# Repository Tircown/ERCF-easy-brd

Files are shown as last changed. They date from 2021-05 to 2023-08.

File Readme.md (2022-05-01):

# ERCF EASY BRD

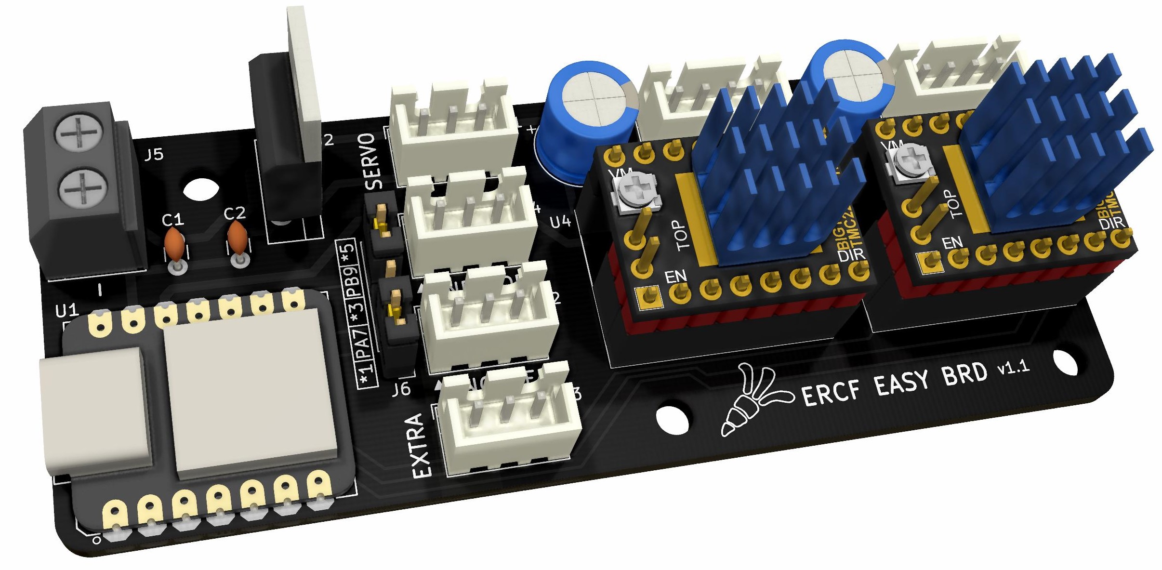
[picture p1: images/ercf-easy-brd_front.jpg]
ERCF front picture


**Be careful not to invert polarity in the screw terminal or it may damage the board and even more.**

**Do not use the servo connector as an input or do it at your own risk.\
Voltage input connected to general I/O pins may cause chip damage if it' higher than 3.3V .**

## BOM
Component | Position
------------ | -------------
Resistor 10K | R1, R2, R3, R4
Capacitor ceramic 0.33uF 25V | C1
Capacitor ceramic 0.1uF 25V | C2
Capacitor 100uF 25V | C3, C4
2P Screw terminal P=5.08 | J5
3P JST-XH male P=2.54 | J1, J2, J3, J4
4P JST-XH male P=2.54 | J6, J7
8P Header socket P=2.54 | *4x for U4 and U3*
2P Header socket P=2.54 | *1x for U4*
5P Header pin P=2.54 | J6
7P Header socket female P=2.54 | *(optionnal) 2x for Seeeduino XIAO*
Seeeduino XIAO or Adafruit QT Py (same footprint & pinout)| U1
Voltage regulator L7805CV | U2
SilentStepStick TMC2209 | U3, U4
Jumper P=2.54 | *2x for J6*
Heatsink for TO-220 | *(recommended) 1x for the L7805CP (1)*

*(1) You will need to bend a fin and remove the pin of the TO-220 heatsink. Make sure the PCB has no bare traces underneath or apply an insolator before (i.e. piece of chattertone).*

## Configure the MCU - Seeeduino XIAO
* Install bossac (version ≥1.8)
```
sudo apt install libreadline-dev libwxgtk3.0-*
git clone https://github.com/shumatech/BOSSA.git
cd BOSSA
make
sudo cp bin/bossac /usr/local/bin
```
* Prepare the firmware
```
cd ~/klipper
make menuconfig
```
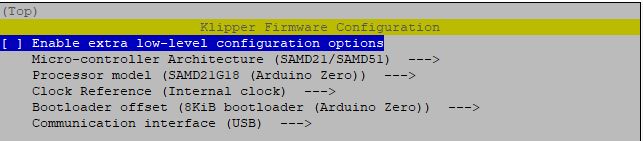
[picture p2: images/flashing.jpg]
Menuconfig instructions

```
make clean
make
```
* Flashing the Seeeduino XIAO
Connect the Seeeduino XIAO to your raspberry if it's not already done.
Get the port of the XIAO, i.e. `ls /dev/tty*`, and modify the default `/dev/ttyACM1` in the command line bellow.
Use tweezers or short lines to short the RST pins in the diagram twice. The orange LED lights flicker on and light up. Then send in the next few seconds this command line matching your port.
```
sudo /usr/local/bin/bossac -i -d -p /dev/ttyACM1 -e -w -v -R --offset=0x2000 out/klipper.bin
```

More informations on how to reset for flashing:\
https://wiki.seeedstudio.com/Seeeduino-XIAO/#enter-bootloader-mode

## Klipper configuration
See [ercf_hardware.cfg](config/Seeeduino%20XIAO%20-%20SAMD21G18/ercf_hardware.cfg) for the Seeeduino XIAO (most common solution)
Other microcontrollers configurations are available in config/

## Get the PCB Board
If you want to support my work: https://www.pcbway.com/project/shareproject/ERCF_EASY_BRD.html \
*note: default setting is "HASL lead free" but if it doesn't matter to you, just change this option to get more affordable boards.*

Or just download the Gerber files and upload it to the manufacturer of your choice.

## Dimensions
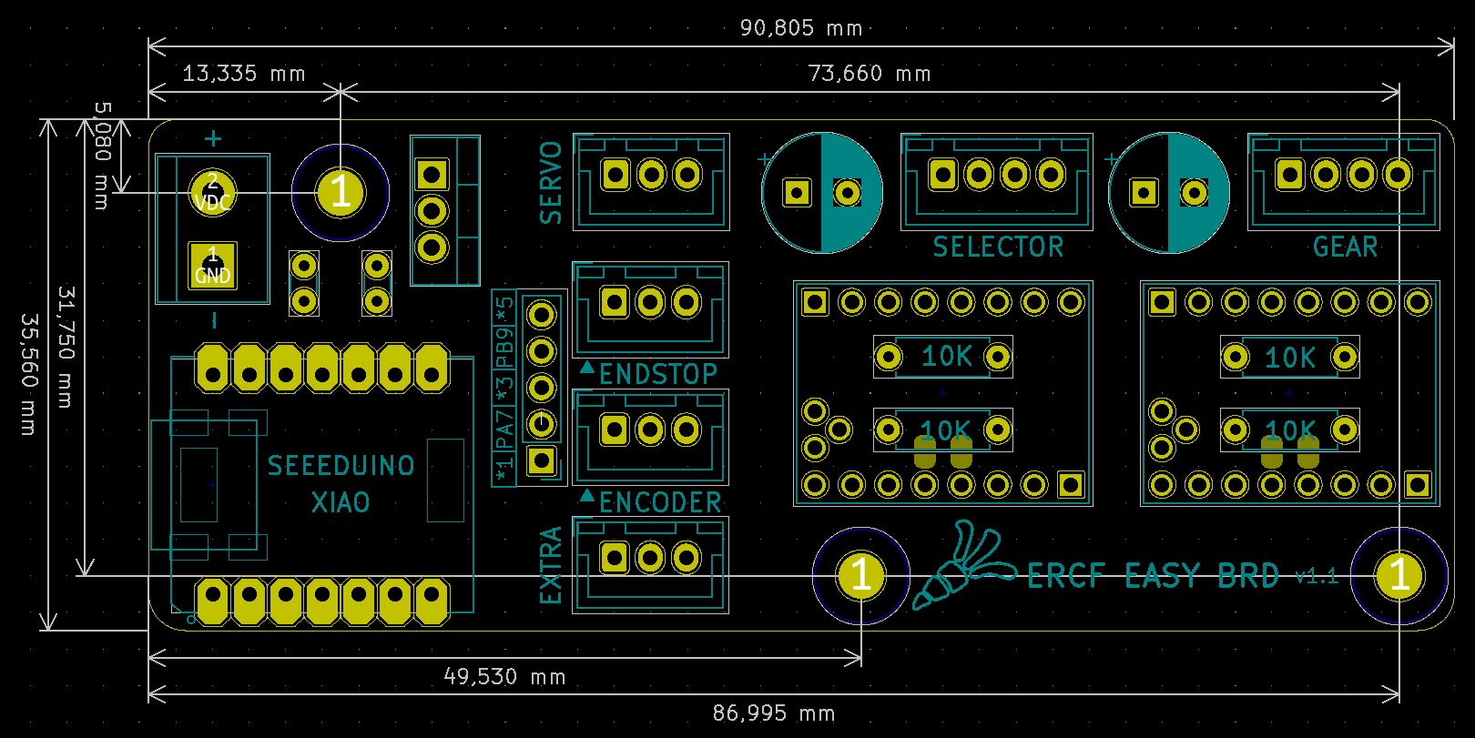
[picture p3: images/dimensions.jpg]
ERCF dimensions picture


## More pictures
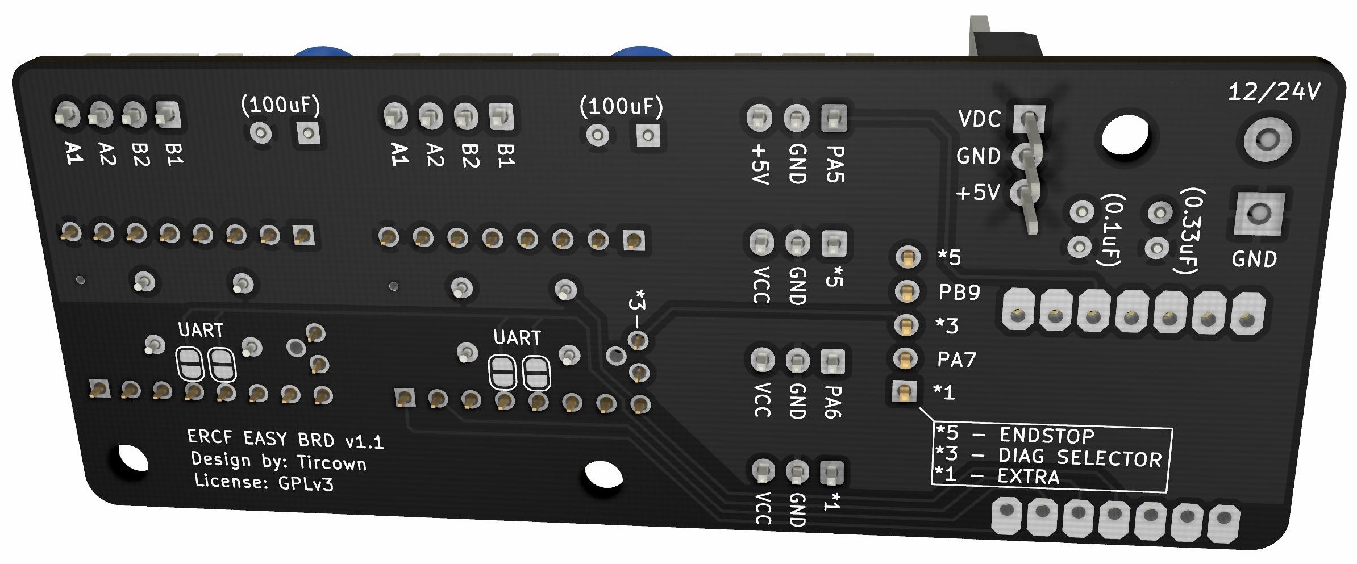
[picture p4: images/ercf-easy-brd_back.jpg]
ERCF back picture

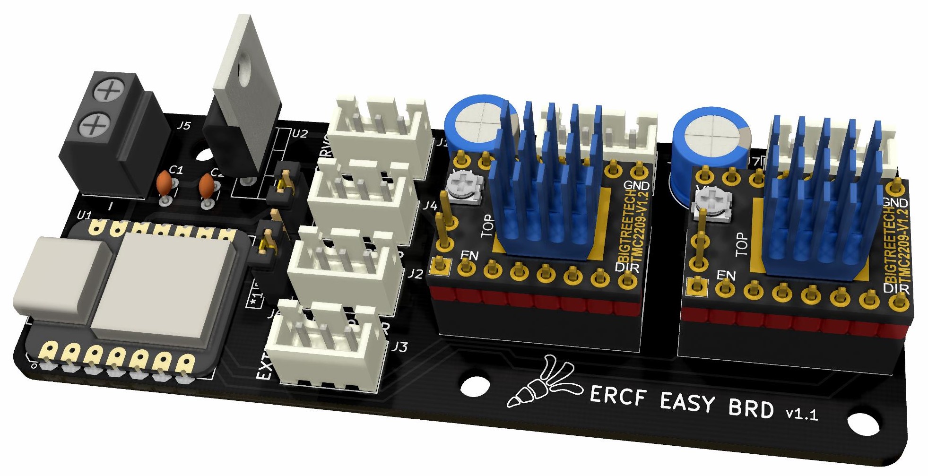
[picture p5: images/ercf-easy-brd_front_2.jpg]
ERCF front picture


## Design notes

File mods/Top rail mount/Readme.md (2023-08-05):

# ERCF EASY BRD MOD : Top rail mount
Author: NyxCode
- [x] Tested

Mounting plate for bolting the PCB to the top of two 2020 extrusions.

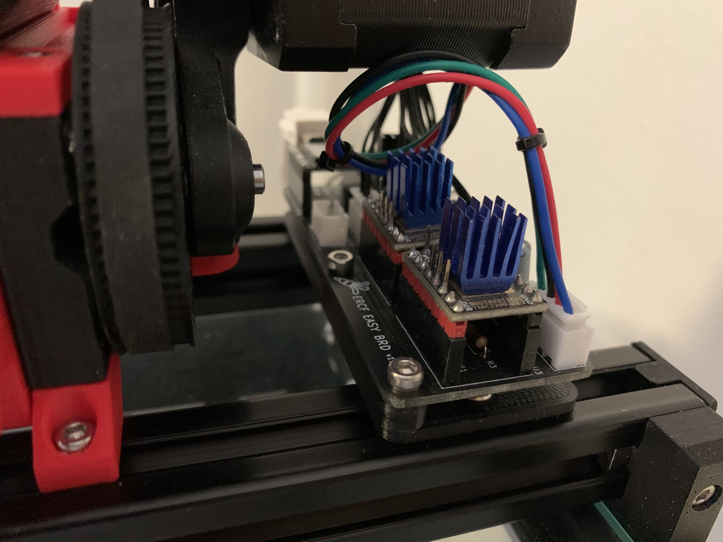
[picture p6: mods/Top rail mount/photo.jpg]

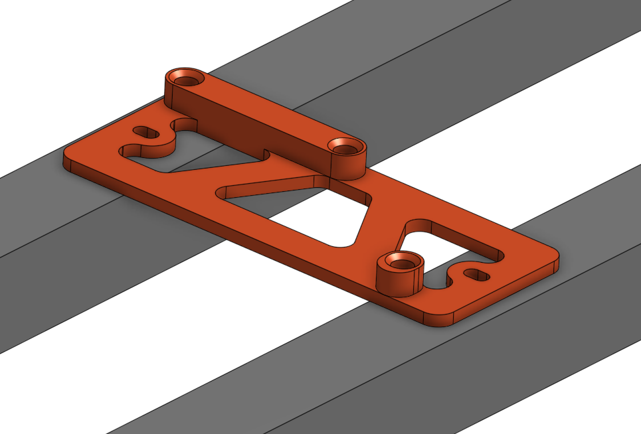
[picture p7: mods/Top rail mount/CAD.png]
CAD


## BOM
- 2 M3x6 BHCS
- 2 M3 T-nuts
- 3 Heatset inserts
- 3 M3x6 BHCS/SHCS

## Instructions
1. Insert the heatset inserts into the printed mounting plate
2. Bolt the mounting plate to the two 2020 extrusions using the two **M3x6 BHCS** and the two **T-nuts**
3. Secure the PCB to the mounting plate using the three **M3x6**

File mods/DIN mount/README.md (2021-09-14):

# ERCF EASY BRD MOD : DIN Mount
Author: mvieleers

Sturdy DIN rail mount for the ERCF Easy Board.\

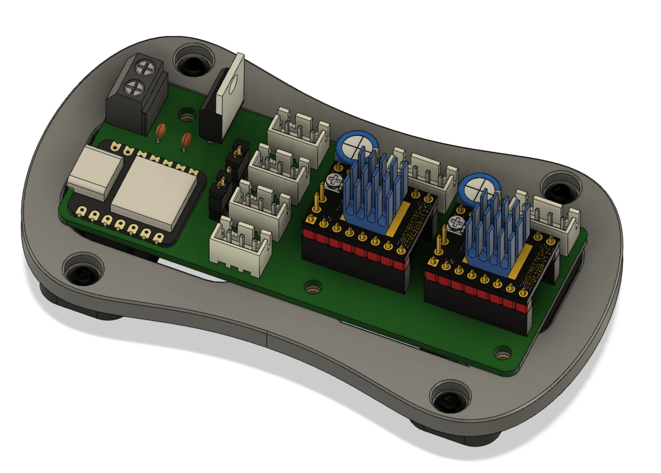
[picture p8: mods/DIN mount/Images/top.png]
Top View

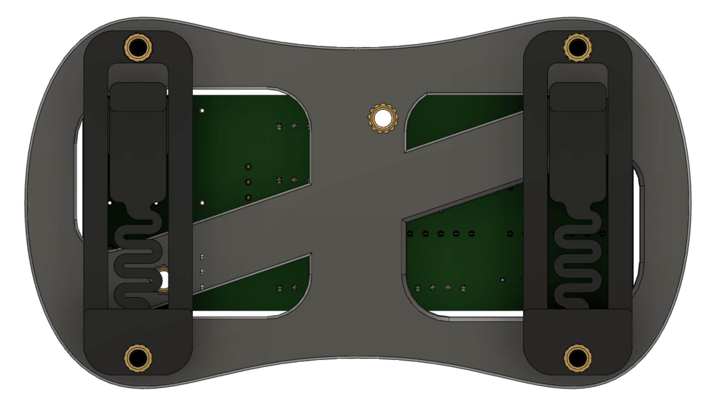
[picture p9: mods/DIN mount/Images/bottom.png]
Bottom View


## Printed Parts
Part|QTY
|:---:|:---:|
DIN Rail Clamp|2
PCB Mount|1

## Hardware
Part|QTY
|:---:|:---:|
M3x6 BHCS or SHCS|3
M3x6 BHCS|4
M3x5x4 heatset inserts (Voron Standard)|7

## Changelog
09-14-2021 | Initial version

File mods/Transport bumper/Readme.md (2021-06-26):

# ERCF EASY BRD MOD : Transport bumper
Author: Tircown
- [x] Tested

Protective bumper to send a complete ERCF board.\
Do not solder the voltage regulator L7805CP since it protrude too much. There is a slot on the side for including it in the package (on the carrot logo).

## Changelog
06-26-2021 | Initial version

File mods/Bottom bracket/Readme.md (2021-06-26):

# ERCF EASY BRD MOD : Bottom bracket
Author: Tircown
- [x] Tested

Low profile bracket.
Place the PCB board as low as possible while being flush with the bottom of the 2020 aluminium extrusion.

## BOM
- 5 M3x8
- 2 M3 T-nuts

## Instructions
1. Remove the 3 built-in supports
2. Screw the ERCF EASY BRD with 3 M3x8 (self-tapping)
3. Install the bracket on a 2020 aluminium profile with the 2 remaining M3x8 and T-nuts

## Changelog
06-26-2021 | Initial version

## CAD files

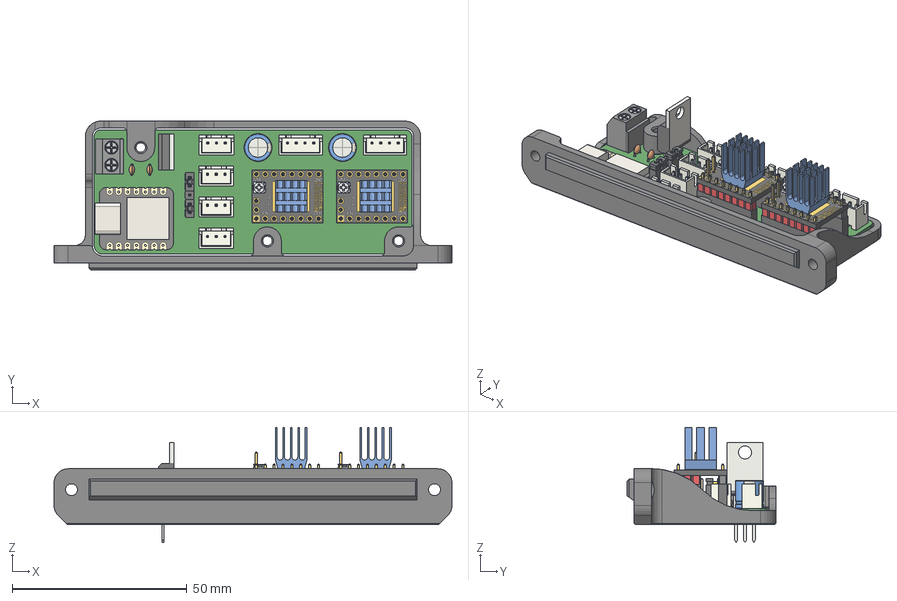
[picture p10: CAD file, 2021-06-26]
mods/Bottom bracket/ercf_easy_brd bracket bottom.step
113.7 x 42.6 x 32.9 mm

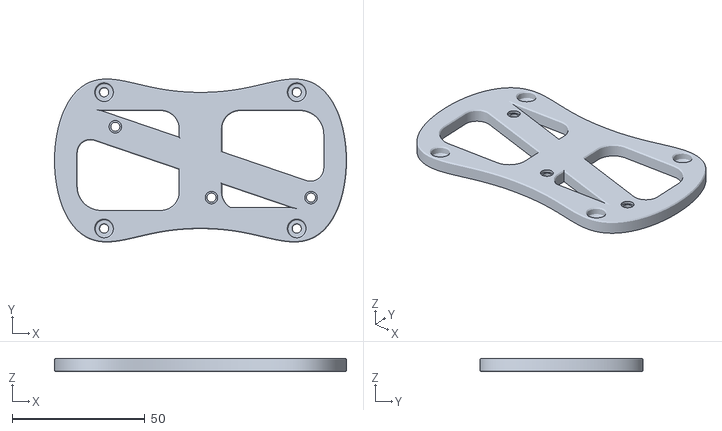
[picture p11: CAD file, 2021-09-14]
mods/DIN mount/STL/ercf-easy_base.stl
109.9 x 61.3 x 5.00

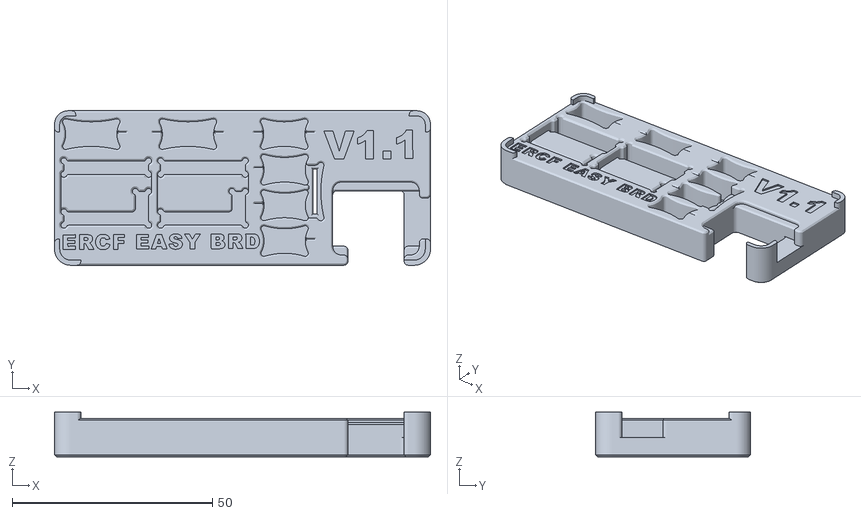
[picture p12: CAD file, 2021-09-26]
mods/Soldering jig/ercf_ez_board soldering jig.stl
93.8 x 38.6 x 11.2

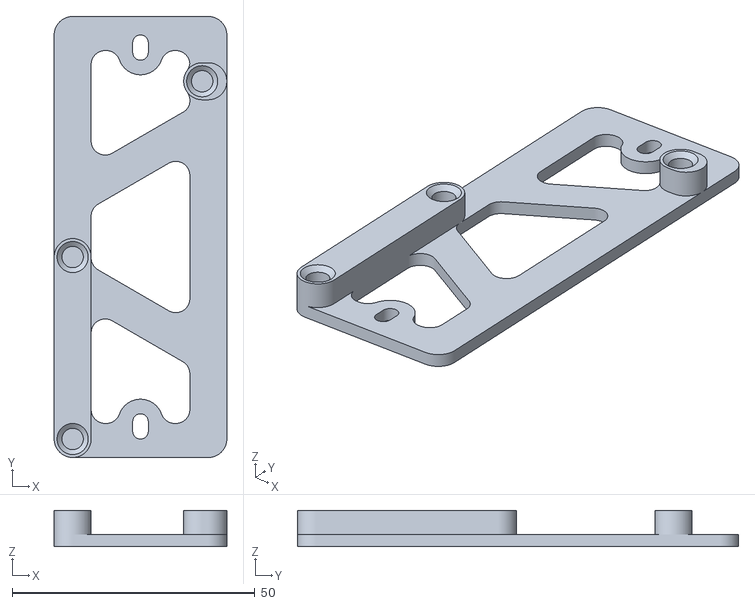
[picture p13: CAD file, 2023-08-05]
mods/Top rail mount/Top rail mount.stl
35.6 x 90.8 x 7.50

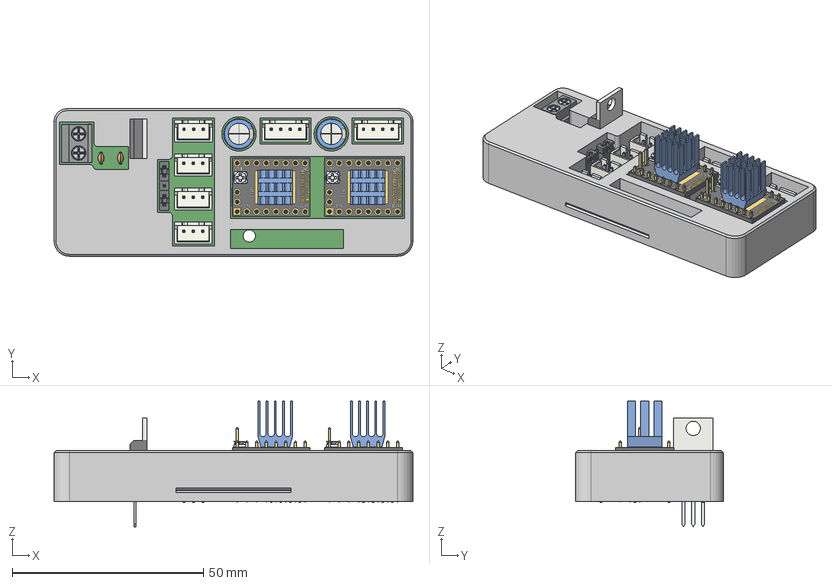
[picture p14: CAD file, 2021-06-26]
mods/Transport bumper/ercf-easy-brd transport bumper.step
93.8 x 38.6 x 32.9 mm

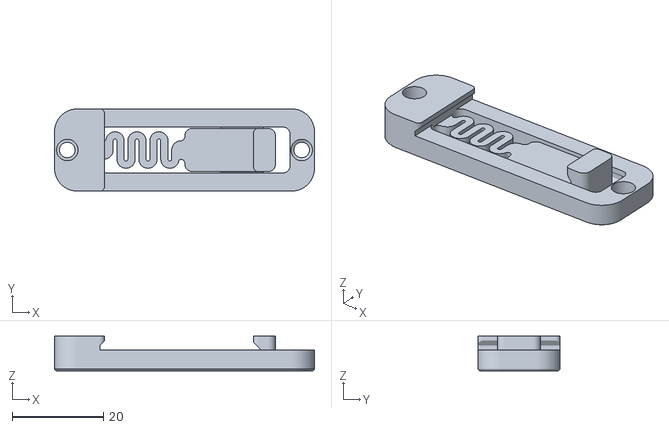
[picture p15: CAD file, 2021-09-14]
mods/DIN mount/STL/din_rail_clamp_x2.stl
56.9 x 18.0 x 7.60

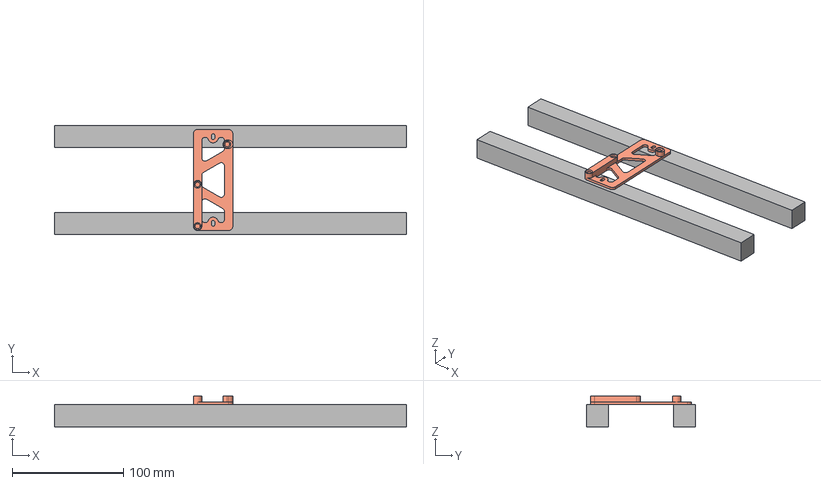
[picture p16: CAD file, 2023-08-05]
mods/Top rail mount/CAD.step
316.5 x 98.0 x 27.5 mm

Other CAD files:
mods/Soldering jig/ercf-easy-brd soldering jig.step
mods/Bottom bracket/ercf_easy_brd bracket bottom.stl
mods/Transport bumper/ercf-easy-brd transport bumper.stl

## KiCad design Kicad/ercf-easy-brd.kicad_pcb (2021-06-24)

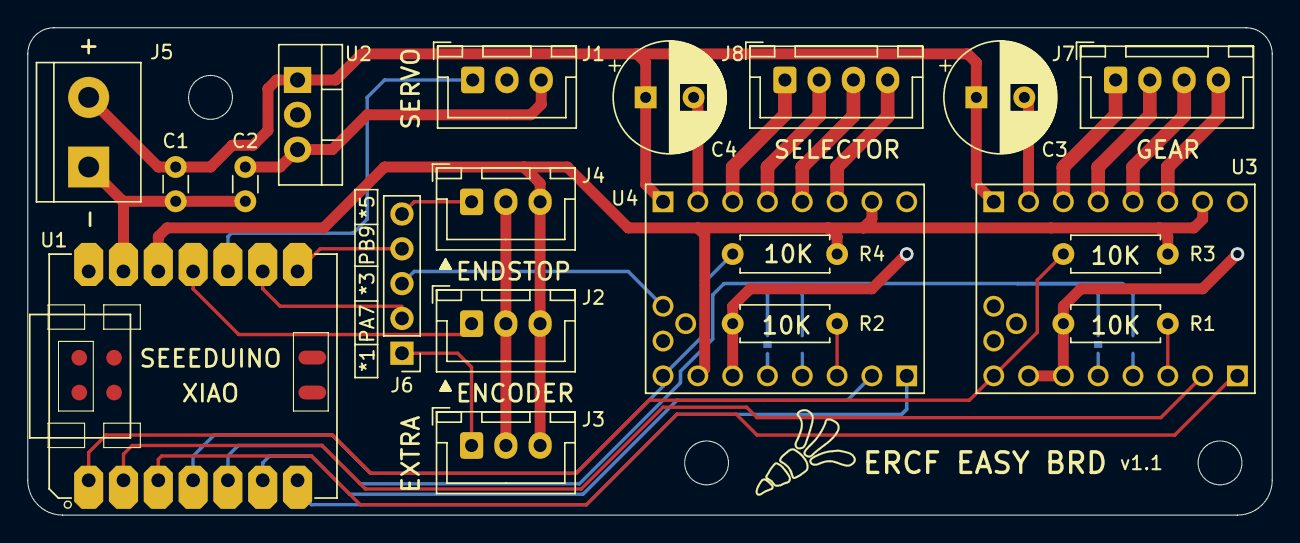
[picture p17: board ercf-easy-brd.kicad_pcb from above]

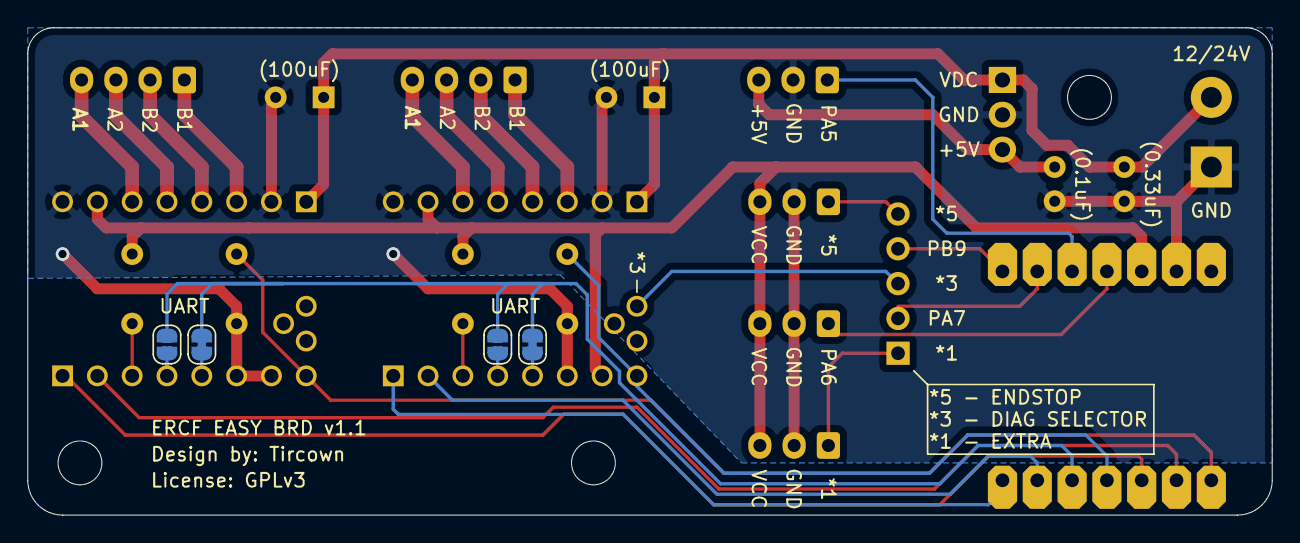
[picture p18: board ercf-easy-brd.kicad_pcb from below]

Board: 2 copper layers, 90.8 x 35.6 mm, 27 parts (4 on the bottom side), 32 nets.

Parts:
C1: 0.33uF; C_Disc_D3.0mm_W1.6mm_P2.50mm
C2: 0.1uF; C_Disc_D3.0mm_W1.6mm_P2.50mm
C3, C4: 100uF; CP_Radial_D8.0mm_P3.50mm
H1, H2, H3: MountingHole; MountingHole_3.2mm_M3
J1, J2, J3, J4: Conn_01x03_Male; JST_XH_B3B-XH-A_1x03_P2.50mm_Vertical
J5: Screw_Terminal_01x02; TerminalBlock_bornier-2_P5.08mm_2
J6: Conn_01x05_Male; PinHeader_1x05_P2.54mm_Vertical_2
J7, J8: Conn_01x04_Male; JST_XH_B4B-XH-A_1x04_P2.50mm_Vertical
JP7, JP9: Jumper_NO_Small; SolderJumper-2_P1.3mm_Open_RoundedPad1.0x1.5mm
JP8, JP10: Jumper_NC_Small; SolderJumper-2_P1.3mm_Bridged_RoundedPad1.0x1.5mm
R1, R2, R3, R4: 10k; R_Axial_DIN0207_L6.3mm_D2.5mm_P7.62mm_Horizontal
U1: SeeeduinoXIAO; SeeeduinoXIAO-MODULE14P
U2: L7805; TO-220-3_Vertical
U3, U4: TMC2209_SILENTSTEPSTICK; MODULE_TMC2209_SILENTSTEPSTICK

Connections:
+3V3: J2.3, J3.3, J4.3, R3.2, R4.2, U1.12, U3.JP2_7, U4.JP1_7, U4.JP2_7
+5V: C2.1, J1.3, U2.3
ENCODER: J2.1, U1.11
EXTRA: J6.2, U1.9
G-DIR: U1.3, U3.JP1_1
G-EN: R3.1, U1.1, U3.JP1_8
G-STEP: U1.2, U3.JP1_2
GND: C1.2, C2.2, C3.2, C4.2, J1.2, J2.2, J3.2, J4.2, J5.1, R1.2, R2.2, U1.13, U2.2, U3.JP1_6, U3.JP1_7, U3.JP2_2, U3.JP2_8, U4.JP1_6, U4.JP2_2, U4.JP2_8
unnamed: J3.1, J6.1
unnamed: J4.1, J6.5
unnamed: J6.3, U4.JP4_1
unnamed: J7.1, U3.JP2_5
unnamed: J7.2, U3.JP2_4
unnamed: J7.3, U3.JP2_3
unnamed: J7.4, U3.JP2_6
unnamed: J8.1, U4.JP2_5
unnamed: J8.2, U4.JP2_4
unnamed: J8.3, U4.JP2_3
unnamed: J8.4, U4.JP2_6
unnamed: JP7.1, U3.JP1_4
unnamed: JP8.2, U3.JP1_5
unnamed: JP9.1, U4.JP1_4
unnamed: JP10.2, U4.JP1_5
unnamed: R1.1, U3.JP1_3
unnamed: R2.1, U4.JP1_3
S-DIR: U1.7, U4.JP1_1
S-EN: R4.1, U1.4, U4.JP1_8
S-MIN: J6.4, U1.8
S-STEP: U1.6, U4.JP1_2
SERVO: J1.1, U1.10
UART: JP7.2, JP8.1, JP9.2, JP10.1, U1.5
VDC: C1.1, C3.1, C4.1, J5.2, U2.1, U3.JP2_1, U4.JP2_1

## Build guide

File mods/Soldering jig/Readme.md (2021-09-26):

# ERCF EASY BRD MOD : Soldering Jig
Author: Tircown 
Thank you to Robertt for the request, tests and feedbacks (and photos).
- [x] Tested

## Instructions
1. Pre-install in the jig:
  * 4x 3P JST-XH
  * 2x 4P JST-XH
  * 4x 8P Header sockets
  * 2x 2P Header sockets
  * 1x 5P Header pins (jumpers removed)
  * Seeeduino XIAO (if you want to solder the castellated holes)
2. (optionnal) pre-install on the PCB the 4x 10Kohms resistors.
3. Place the PCB on top of the jig.
4. Ready to solder.
5. _The others components still need to be soldered afterward._

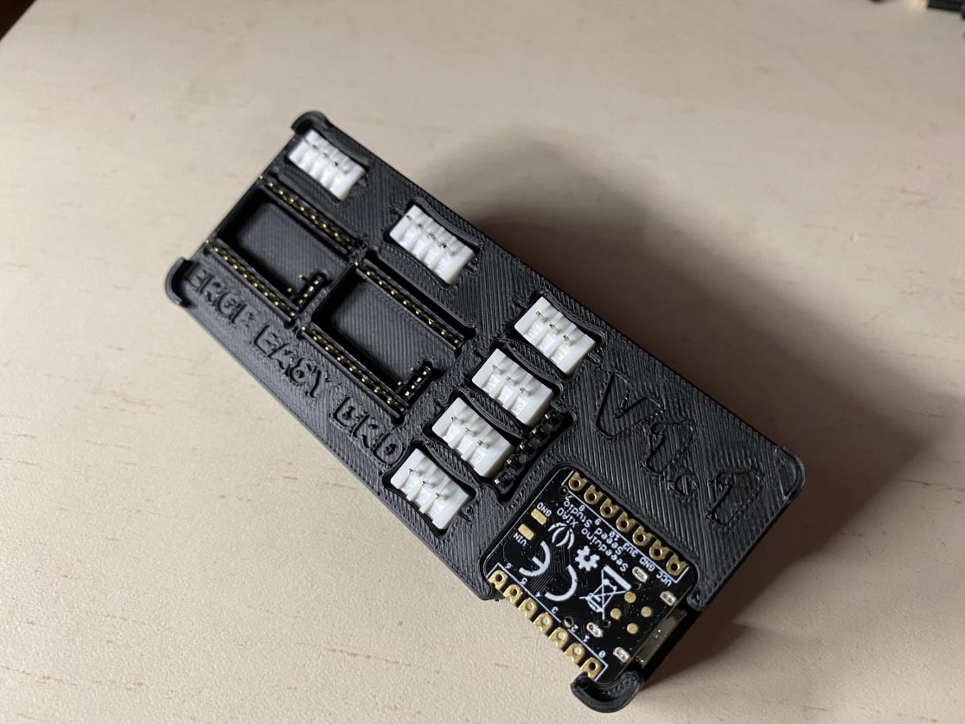
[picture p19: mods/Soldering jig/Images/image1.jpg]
Preload

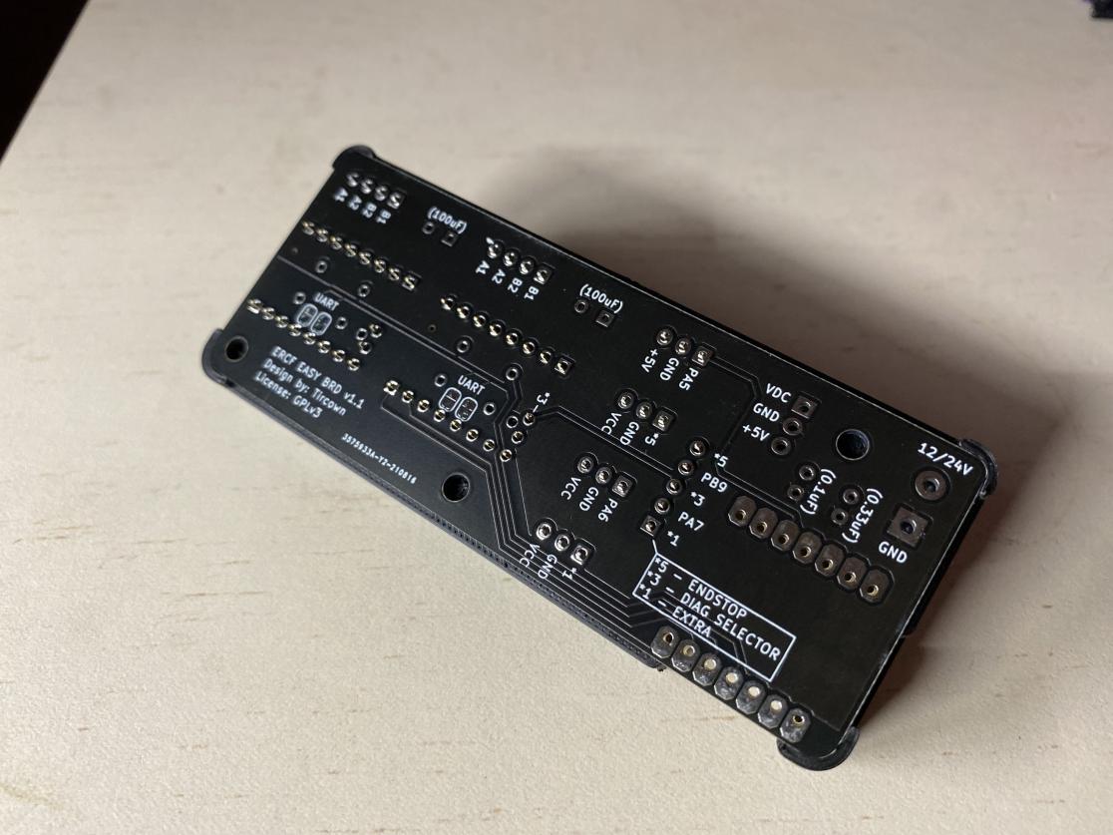
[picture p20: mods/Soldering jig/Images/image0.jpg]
Board


## Changelog
09-26-2021 | Initial version

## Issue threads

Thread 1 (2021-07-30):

Voltage

cdkonecny, 2021-07-30:
Should voltage be stepped down to 12v for input on this board?
I have references to overheating at 24v but information is vague and unclear whether it applies to this version.

Tircown, 2021-07-30:
- At 12V the ERCF-EASY-BRD works fine, without issues.
- At 24V you will need a good heatsink and to be sure that the servo motor doesn't block otherwise it draws more current and the voltage regulator goes into thermal protection. More test are still needed to know exactly when the heatsink is enough and when it's not.
- Another option is to deliver 24V to the board for the steppers motors and wire a buck converter in place of the L7805 to get 5V for the servo motor.

cdkonecny, 2021-07-30:
Very helpful.   Thank you

Closed 2021-07-30.

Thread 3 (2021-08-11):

10K resistor question

troyster980, 2021-08-11:
on the 10K resistors for the stepper motor drivers do they have power rating on them?  if not is there a power rating that you would suggest.  I ask because i can find 1/2, 1/4, 1/6, and 1/8 watt 10k Ohm resistors

Tircown, 2021-08-12:
I use 1/4W. There is not a lot of current that pass through them.

Closed 2021-08-22.

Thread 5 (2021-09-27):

Question - Voltage regulator L7805

mdsamir150790, 2021-09-27:
with towerpro mg90s servo in the ercf v1.1, id is possible to switch L7805CP with L7805CV ?

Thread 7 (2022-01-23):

Cannot configure toolhead pin on board

Makarintosh, 2022-01-23:
I've built the ERCF using an Easy BRD 1.1 but I cannot find the pin that uses the "Extra" pin header on the board. The config shows the pin for SKR 1.4 but documents say I can use the "Extra" header.

Makarintosh, 2022-01-23:
```
## Enraged Rabbit : Carrot Feeder V1.1 hardware config file
# Values are an example for voron 2.4 with 2 SKR1.4

[mcu ercf]
serial: /dev/serial/by-id/usb-Klipper_samd21g18a_0D55BD144E34555020312E3132040DFF-if00

# Carrot Feeder 5mm D-cut shaft
# Example for an SKR 1.4 Board (E1 on the XY mcu)
[manual_stepper gear_stepper]
step_pin: ercf:PA4
dir_pin: ercf:PA10
enable_pin: !ercf:PA2
rotation_distance: 22.6789511	#Bondtech 5mm Drive Gears
gear_ratio: 80:20
microsteps: 16
full_steps_per_rotation: 200	#200 for 1.8 degree, 400 for 0.9 degree
velocity: 35
accel: 150
#Right now no pin is used for the endstop, but we need to define one for klipper. So just use a random, not used pin
endstop_pin: ^ercf:PA7

[tmc2209 manual_stepper gear_stepper]
# Adapt accordingly to your setup and desires
# The default values are tested with the BOM NEMA14 motor
# Please adapt those values to the motor you are using
# Example : for NEMA17 motors, you'll usually set the stealthchop_threshold to 0
# and use higher current
uart_pin: ercf:PA8
uart_address: 0
interpolate: True
run_current: 0.40
hold_current: 0.1
sense_resistor: 0.110
stealthchop_threshold: 500

# Carrot Feeder selector
# Example for an SKR 1.4 Board (Z1 on the XY mcu)
[manual_stepper selector_stepper]
step_pin: ercf:PA9
dir_pin: ercf:PB8
enable_pin: !ercf:PA11
microsteps: 16
rotation_distance: 40
full_steps_per_rotation: 200	#200 for 1.8 degree, 400 for 0.9 degree
velocity: 200
accel: 600
endstop_pin: ^!ercf:PB9

[tmc2209 manual_stepper selector_stepper]
uart_pin: ercf:PA8
uart_address: 1
run_current: 0.55
interpolate: True
sense_resistor: 0.110
stealthchop_threshold: 5000

# Values are for the MG90S servo
[servo ercf_servo]
pin: ercf:PA5
maximum_servo_angle: 180
minimum_pulse_width: 0.00085
maximum_pulse_width: 0.00215

[duplicate_pin_override]
pins: ercf:PA6
# Put there the pin used by the encoder and the filament_motion_sensor
# It has to be the same pin for those 3

[filament_motion_sensor encoder_sensor]
switch_pin: ^ercf:PA6
pause_on_runout: False
detection_length: 4.0
extruder: extruder
# runout_gcode: ERCF_ENCODER_MOTION_ISSUE

[filament_switch_sensor toolhead_sensor]
pause_on_runout: False
switch_pin: ^P1.27
```

My current settings. I have tried cycling through different pin numbers but no luck.

Tircown, 2022-01-23:
1/ Change the gear_stepper's endstop_pin to an unused but existing pin on the Seeeduino XIAO, PA1 for instance.
2/ Put the jumper on the board between 1* and PA7
3/ The pin to set for the extra connector is now `^ercf:PA7`

Makarintosh, 2022-01-23:
Thanks for the help @Tircown.

It didn't help however, Mainsail indicates that the toolhead_sensor is 'detected' but there is no filament at the sensor. I fed some filament in but nothing appears to change. Is there something else I can try?

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

Tircown, 2022-01-23:
The issue is now related to the toolhead sensor itself.
This may be due to the wires, the strength of the magnet, etc.
Voron's discord server, #ercf_questions is a better place to get help.

Closed 2022-01-23.

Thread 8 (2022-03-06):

Flashing failed

schnello, 2022-03-06:
Hello.

I try to flash Klipper to the Seed but it fails always with this error:
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

Make menu config looks correct from my side:
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

Anyone a hint how this issue can be solved.

schnello, 2022-03-13:
Solved:
Use ls -l /dev/serial/by-id/ to if the real ID. In my case /dev/ttyACM0

Then use sudo /usr/local/bin/bossac -i -d -p /dev/ttyACM0 -e -w -v -R --offset=0x2000 out/klipper.bin

Closed 2022-03-13.

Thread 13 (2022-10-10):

Raspberry config for Bossac gives Error, file not found

Toogo, 2022-10-10:
When trying to install, teher are erros saying file does not exists:
So make is not working

sudo apt install libreadline-dev libwxgtk3.0-*
git clone https://github.com/shumatech/BOSSA.git
cd BOSSA
make

Is there a solution so I can let the Rabbit work?

Frank

Tircown, 2022-10-10:
Can you share a screenshot of the console log when doing the setup please. Or at least the exact error message and previous commands.

Closed 2022-10-19.

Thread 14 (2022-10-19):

Unable to read tmc uart 'selector_stepper' register DRV_STATUS

hushilin, 2022-10-19:
The success of “gear_stepper”
Unable to read tmc uart 'selector_stepper' register DRV_STATUS

Tircown, 2022-10-19:
This is not an issue related to the design of the board but a faulty one or the stepper drivers or whatever.
Github is not the right place for your problem, ask for help on the Voron discord, channel ercf please.

Thanks

Closed 2022-10-19.

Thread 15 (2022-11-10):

tophat servo

Outofbox11, 2022-11-10:
having issue with servo not working with easy brd v1.1
there is 5V but only hear slight buzz sound and no movement when commanded.
thought it was servo and tried new ones and same issue.
reflash & reinstall didn't work either.  is there something I am missing?

Outofbox11, 2022-11-10:
figured it out.  servo section of the board is bad.  reconfigured and connected servo to my spider board and it works fine.

Closed 2022-11-10.

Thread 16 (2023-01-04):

Updated bossac installation process/steps documented in Readme.md

heymoe, 2023-01-04:
Changing the current install process for bossac from:

```
sudo apt install libreadline-dev libwxgtk3.0-*
git clone https://github.com/shumatech/BOSSA.git
cd BOSSA
make
sudo cp bin/bossac /usr/local/bin
```

to this:

```
git clone https://github.com/shumatech/BOSSA.git
cd BOSSA
make bossac
sudo cp bin/bossac /usr/local/bin
```
removes the need to install the libreadline-dev and libwgtk3.0-* OS packages that are only needed to compile the GUI BOSSA apps which are not needed to flash firmware to the Seeeduino XIAO board. The updated make command ("make bossac") will just compile the bossac command line binary and nothing else. This will also speed up the build/make process since the GUI BOSSA apps won't get built.

I followed the updated process and was successful at flashing my ERCF Easy Board with Klipper.

katanabladesman, 2024-06-21:
Just wanted to say thank you for sharing this, this fixed it for me too.

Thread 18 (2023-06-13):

different wiring MS1 / MS2

Fragmon, 2023-06-13:
Hello,

i look into the pcb and see that one tmc driver is set gnd/gnd (8 Microsteps) and the other gnd/vcc (16 Microsteps. But both stepper are set with 16 microsteps in the config. Can you explain, why you set the tmc to this different microsteps?

Tircown, 2023-08-05:
Hello,
It's wired for UART, not standalone mode. MS1 and MS2 are used for UART address and so are different for each driver. Microsteps are set by firmware config.

Closed 2023-08-05.

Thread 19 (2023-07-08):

Unbrick Seeduino

lettore, 2023-07-08:
As everyone knows it's easy to brick a Seeduino as the chip doesn't have a separate USB controller.
The 2 pins needed to reflash the bootloader are located on the back of the board, with this design they are unreachable and the only solution is to desolder the entire board or throw away all.
I'm wondering why the Seeduino is not fixed to the board through a removable socket, or at least provide two holes on the mainboard to reach that pads.
This is unbelievable.

Tircown, 2023-08-05:
The footprint has holes and the BOM contains optional 7P Header socket female (the male included with the Seeeduino XIAO), so you have the choice to solder directly with castellated pin or removable.
Also some vendors sales with this pins and a removable Xiao.

lettore, 2023-08-05:
As you say optional you don't understand that this is critical feature, to be able to reflash a bricked seeduino. Vendors will take this optional as an option ofcourse, why they should spend more for something that is optional for the designer. Anyway I bought a ERCF-Easy-brd can board that is based on RPI 2040 and works marvelous not like your design. I just wasted 30 Euro for a bricked board. Thank you

Closed 2023-08-05.

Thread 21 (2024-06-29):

Cannot get board to flash.

utzy79, 2024-06-29:
Cannot get board to flash.
I have followed both the directions in the main page and in the issues page, but keep getting operation failed when trying to flash.
Cant work out what I am doing wrong, have touched on the reset pins twice to make the orange light light up but sill doesnt work.
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

utzy79, 2024-06-29:
Nevermind, changed usb cables and it worked

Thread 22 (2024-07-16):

Need pinout for "Extra" port

Beta1492, 2024-07-16:
I'm trying to add a toolhead sensor to my ERCF using the "Extra" port on the Easy BRD, but I cannot find the pinout anywhere.
Any help would be appreciated!

Beta1492, 2024-07-16:
Found it! PA7
For anyone using the Easy BRD with Happy Hare, you need to use mmu:PA7 to call the pin.

f00d4tehg0dz, 2024-08-14:
> Found it! PA7 For anyone using the Easy BRD with Happy Hare, you need to use mmu:PA7 to call the pin.
I'm having trouble getting a servo for the filament cutter to respond from PA7. I can make a diode LED turn on and off. But I can't get my servo to turn. How did you setup PA7 pin layout?
For example, I have a DC 12v to a buck converter to 5v which runs directly to the servo, and the data/signal cable running to the PA7 1st pin out of 3.

Closed 2024-07-16.

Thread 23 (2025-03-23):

Got this issue: Could not exclusively lock port /dev/serial/by-id/usb-Klipper_samd21g18a

Riceball4all, 2025-03-23:
[Errno 11] Could not exclusively lock port /dev/serial/by-id/usb-Klipper_samd21g18a_524D7BA44134555020312E30352D14FF-if00: [Errno 11] Resource temporarily unavailable

[klippy.log](https://github.com/user-attachments/files/19406502/klippy.log)

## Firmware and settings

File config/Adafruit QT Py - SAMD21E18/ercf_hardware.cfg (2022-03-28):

## Enraged Rabbit : Carrot Feeder config file for ERCF EASY BRD v1.1

# This file contains common pin mappings for the Adafruit Qt Py (SAMD21 version).
# To use this config, the firmware should be compiled for the
# SAMD21E18 with "Internal clock" and a "8KiB bootloader".

# This config sample assume you set the two J6 jumpers on 1-2 and 4-5, i.e. [..].[..]

[mcu ercf]
serial: /dev/serial/by-id/usb-Klipper_samd21g18a_B75E8EA94C51535020312E372C1F18FF-if00

# Carrot Feeder 5mm D-cut shaft
[manual_stepper gear_stepper]
step_pin: ercf:PA3
dir_pin: ercf:PA4
enable_pin: !ercf:PA2
rotation_distance: 22.6789511	# Bondtech 5mm Drive Gears
gear_ratio: 80:20
microsteps: 16                  # Please do not go higher than 16, this can cause 'MCU Timer too close' issues under Klipper
full_steps_per_rotation: 200    # 200 for 1.8 degree, 400 for 0.9 degree
velocity: 35
accel: 150
# Right now no pin is used for the endstop, but we need to define one for klipper. So just use a random, not used pin
endstop_pin: ^ercf:PA1          # unused pin on the Qt Py

[tmc2209 manual_stepper gear_stepper]
# Adapt accordingly to your setup and desires
# The default values are tested with the BOM NEMA14 motor
# Please adapt those values to the motor you are using
# Example : for NEMA17 motors, you'll usually set the stealthchop_threshold to 0
# and use higher current
uart_pin: ercf:PA16
uart_address: 0
interpolate: True
run_current: 0.4
hold_current: 0.1
sense_resistor: 0.110
stealthchop_threshold: 500

# Carrot Feeder selector
[manual_stepper selector_stepper]
step_pin: ercf:PA17
dir_pin: !ercf:PA6
enable_pin: !ercf:PA5    
rotation_distance: 40
microsteps: 16                  # Please do not go higher than 16, this can cause 'MCU Timer too close' issues under Klipper
full_steps_per_rotation: 200	  # 200 for 1.8 degree, 400 for 0.9 degree
velocity: 200
accel: 600
endstop_pin: ^!ercf:PA7
#endstop_pin: tmc2209_selector_stepper:virtual_endstop

[tmc2209 manual_stepper selector_stepper]
uart_pin: ercf:PA16
uart_address: 1
run_current: 0.55
interpolate: True
sense_resistor: 0.110
stealthchop_threshold: 5000
# Uncomment the lines below if you want to use sensorless homing for the selector
#diag_pin: ^ercf:PA11           # Set to MCU pin connected to TMC DIAG pin - move the jumper to position 2-3
#driver_SGTHRS: 75              # 255 is most sensitive value, 0 is least sensitive

# Values are for the MG90S servo
[servo ercf_servo]
pin: ercf:PA9
maximum_servo_angle: 180
minimum_pulse_width: 0.00085
maximum_pulse_width: 0.00215

[duplicate_pin_override]
pins: ercf:PA10
# Put there the pin used by the encoder and the filament_motion_sensor
# It has to be the same pin for those 3

[filament_motion_sensor encoder_sensor]
switch_pin: ^ercf:PA10
pause_on_runout: False
detection_length: 10.0
extruder: extruder
# runout_gcode: _ERCF_ENCODER_MOTION_ISSUE

[filament_switch_sensor toolhead_sensor]
pause_on_runout: False
# filament sensor wired to the printer MCU
switch_pin: ^P1.27

# Uncomment the lines below if you want to use the Qt Py LED as a Neopixel
#[neopixel ercf]
#pin: ercf:PA18

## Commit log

2021-05-31 Fix comment on schematic and layout
    Fix comment on schematic and layout
    [ercf-ez-board.kicad_pcb, ercf-ez-board.sch]
2021-05-31 Fix XIAO footprint
    Fix XIAO footprint: one hole smaller
    Rename folder to Kicad
    [ercf-ez-board-B_Cu.gbl, ercf-ez-board-B_Mask.gbs, ercf-ez-board-B_SilkS.gbo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]
2021-06-01 Complete config sample
    Add the multi mcu section
    Edit pins accordingly to the mcu
    Fix the servo pin
    [ercf_hardware.cfg]
2021-06-01 Open 2nd jumper
    Open the jumper for the second UART pin
    [ercf-ez-board-B_Cu.gbl, ercf-ez-board-B_Mask.gbs, ercf-ez-board-B_SilkS.gbo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]
2021-06-01 Fix accidently remove the logo
    Fix accidentally remove the logo
    Minor typo in readme
    [ercf-ez-board-B_Cu.gbl, ercf-ez-board-B_Mask.gbs, ercf-ez-board-B_SilkS.gbo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]
2021-06-17 Fix pin in config
    Fix endstop pin and gear_stepper enable pin in config sample
    [ercf_hardware.cfg]
2021-06-18 PCB v1.1
    PCB v1.1:
    - VCC for endstop, encoder and extra are now 3V3
    - Fix gear stepper ground plane was not connected to GND
    - Improve the tracks width for power and motors
    [ercf-ez-board-B_Cu.gbl, ercf-ez-board-B_Mask.gbs, ercf-ez-board-B_SilkS.gbo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]
2021-06-24 Rename project
    Rename project from ercf-ez-board to ercf-easy-brd to avoid confusion: it is not a TH3D product.
    [ercf-easy-brd-B_Cu.gbl, ercf-easy-brd-B_Mask.gbs, ercf-easy-brd-B_SilkS.gbo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]
2021-06-24 Add Adafruit QT Py and general warnings
    Add Adafruit QT Py to the list of mcu since it can be used as a direct replacement.
    Add warnings for the wiring
2021-06-24 Add PCBWay project link
    Add PCBWay project link
2021-06-26 Mod: bracket bottom
    Bottom bracket mod
    [ercf_easy_brd bracket bottom.step, ercf_easy_brd bracket bottom.stl]
2021-06-26 Mod: Transport bumper
    Transport bumper mod
    [ercf-easy-brd transport bumper.step, ercf-easy-brd transport bumper.stl]
2021-06-26 Fix typo
    Fix typo in bottom bracket and transport bumper readmes
2021-09-14 Initial files upload
    [din_rail_clamp_x2.stl, ercf-easy_base.stl]
2021-09-26 Mod: soldering jig
    Add a mod to help soldering the connectors, XIAO and resistors.
    [ercf-easy-brd soldering jig.step, ercf_ez_board soldering jig.stl]
2021-10-23 - Updated the ercf_hardware.cfg to ercfv1.1 config
    [ercf_hardware.cfg]
2021-10-23 - Typos
    [ercf_hardware.cfg]
2021-11-17 add heatsink in the readme
    Add heatsink in the BOM.
    Add instructions to install the heatsink on the board.
2021-12-08 Update ercf_hardware.cfg
    Remove deprecated settings in ercf_hardware.cfg
    Update the detection_length for the filament_motion_sensor to match the main ERCF repo cfg.
    [ercf_hardware.cfg]
2021-12-08 Update readme: TMC2209
    The easy brd is not compatible with the TMC2208 because of the way it communicates through a single UART wire on different addresses. The TMC2226 should also be compatible according to the datasheet but AFAIK not yet tested. TMC2209 is now officially the spec.
2022-03-28 Move and update ercf_hardware.cfg for the XIAO
    Prepare the folders for multiple mcu
    Update ercf_hardware.cfg for the XIAO.
    [ercf_hardware.cfg]
2022-03-28 Create ercf_hardware.cfg for QT Py
    Create ercf_hardware.cfg for QT Py
    [ercf_hardware.cfg]
2022-03-28 Add Qt Py SAMD21 config
    [ercf_hardware.cfg]
2022-03-28 Remove stepper model
    [ercf_hardware.cfg]
2022-04-07 Change links to the config
    Change the links to the config sample.
    [ercf_hardware.cfg]
2022-04-07 Fix link to config sample
    Fix link to config sample
2023-01-22 add top rail mount mod
    [CAD.step, Top rail mount.stl]

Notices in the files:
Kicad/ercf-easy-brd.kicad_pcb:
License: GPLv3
